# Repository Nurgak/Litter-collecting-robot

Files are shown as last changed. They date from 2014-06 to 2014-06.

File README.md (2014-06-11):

# STI interdisciplinary robot competition

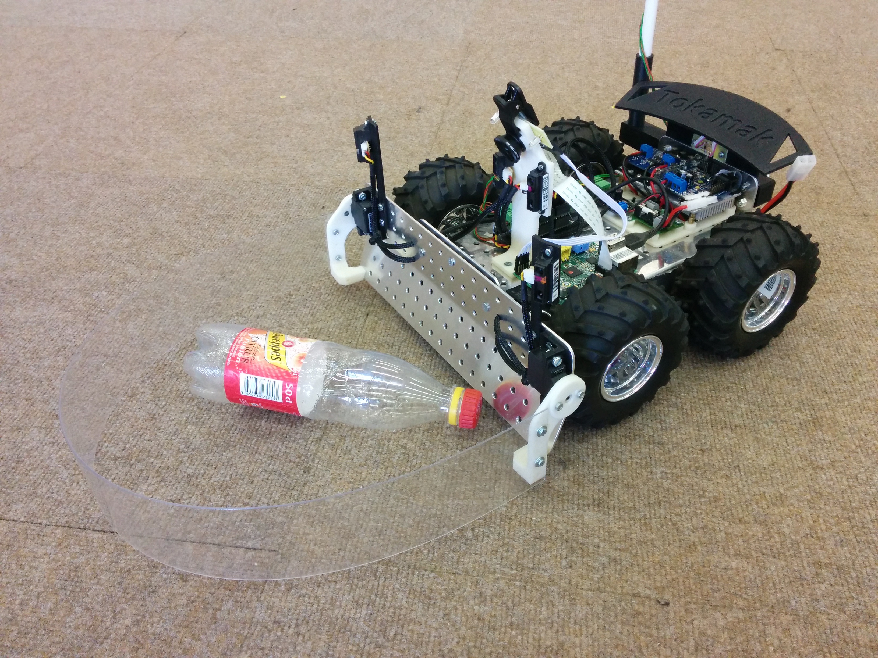
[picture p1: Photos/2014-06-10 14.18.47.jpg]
Tokamak


This project was completed as a Master semester project at [École polytechnique fédérale de Lausanne](http://www.epfl.ch).

* Authors: Karl Kangur, Marcel Starein, Chun Xie
* Assistants: Alessandro Crespi, Gorecki Tomasz
* Professor: Auke Ijspeert

## Abstract

The [STI competition](http://robot-competition.epfl.ch) is a interdisciplinary Master semester project in form of a competition between five teams of three people from different educational backgrounds. The competition's goal is to design and build a litter collecting robot and outperform the other robots. The teams are given funds in order to buy parts, order custom parts from the in-house mechanics or make use of the available 3D printers.

## Project report

The complete project report with all the documentation is in `Documents/Project report.pdf`.

## Video

[**Video of bottle fetching and detection demonstration**](https://www.youtube.com/watch?v=RZNW9JzXmiI)

## Pictures

See under `Photos`.

## Files

* All documents related to the project (rules, deadlines) and the project report itself are in `Documents`
* Documents related to sensors are under `Datasheets`
* First concepts in Google SketchUp, final parts in SolidWorks format and custom PCBs in `Hardware`
* The complete source code for the Raspberry Pi, Arduino code for the [PRsimino](https://github.com/Robopoly/prismino) and the custom WildThumper motor controller are in `Software`
* Pictures of the robot are under `Photos`
* The Webots files for the simulation are in `Webots simulation`

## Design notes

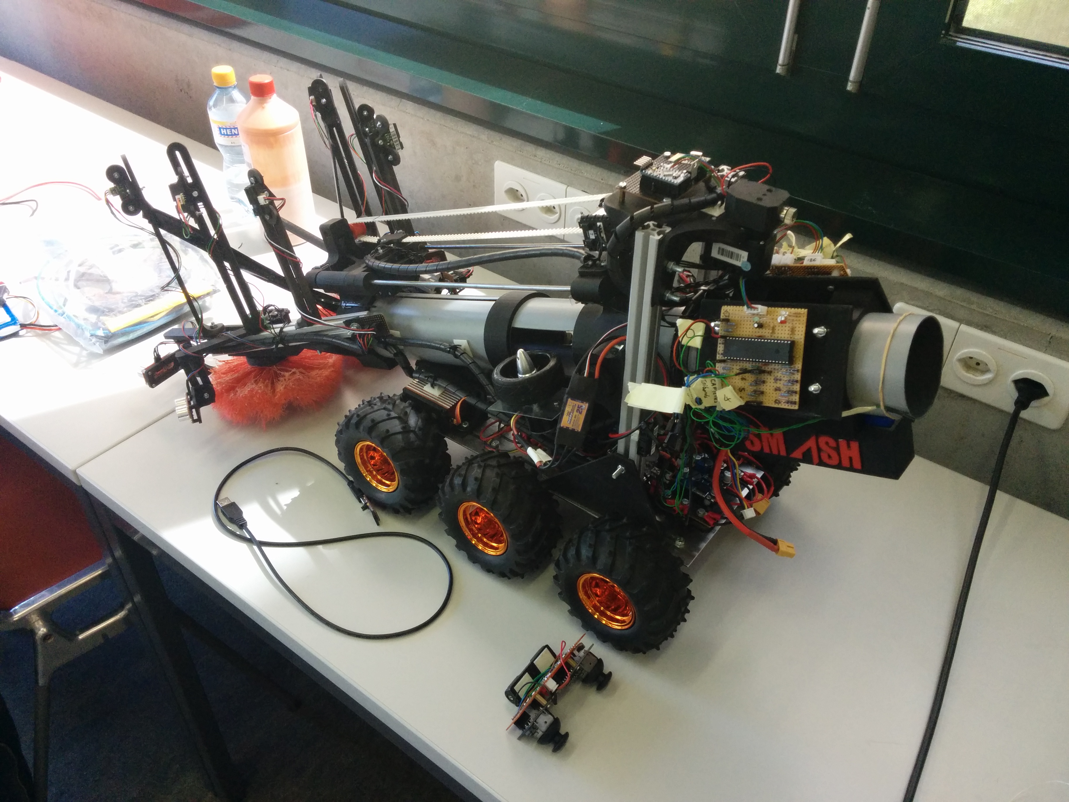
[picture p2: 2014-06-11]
Photos/2014-06-10 11.02.56.jpg

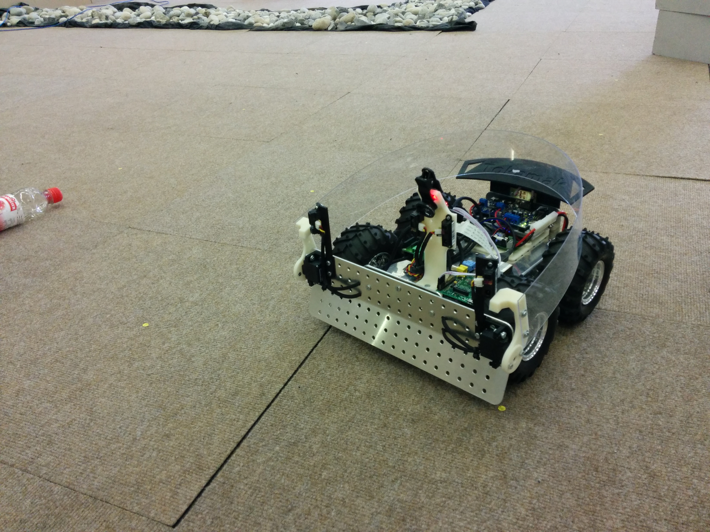
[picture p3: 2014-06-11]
Photos/2014-06-08 19.46.35.jpg

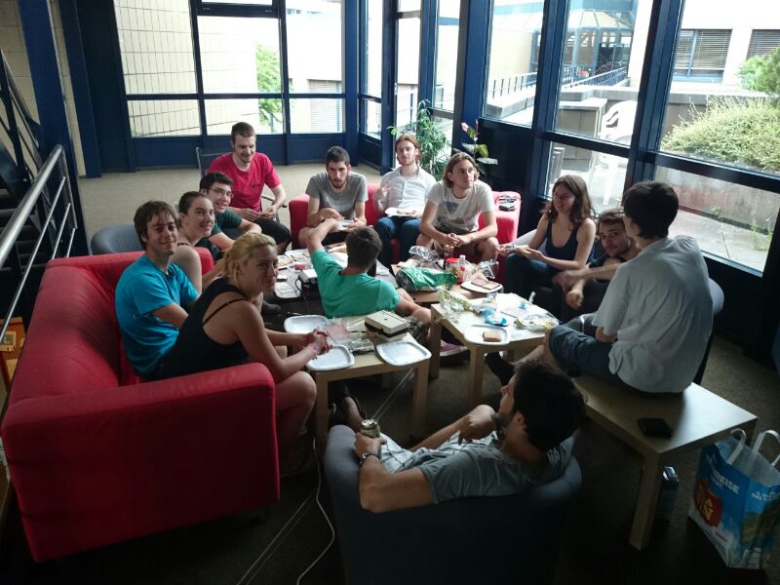
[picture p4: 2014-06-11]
Photos/IMG-20140609-WA0000.jpg

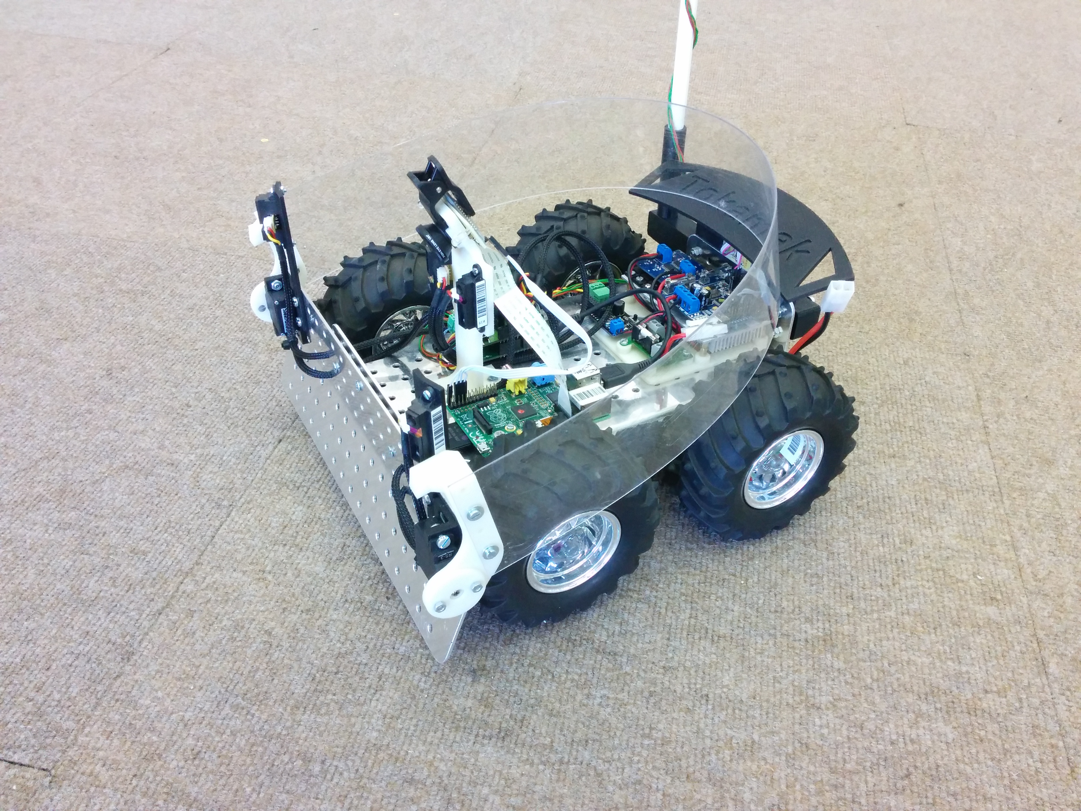
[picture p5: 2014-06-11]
Photos/2014-06-10 14.17.28.jpg

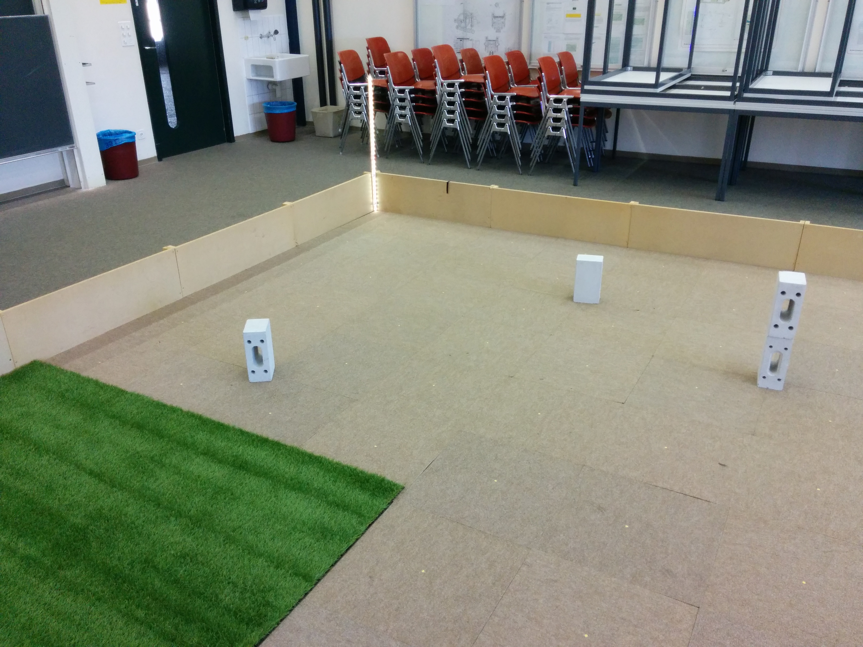
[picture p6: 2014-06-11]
Photos/2014-06-03 10.24.10.jpg

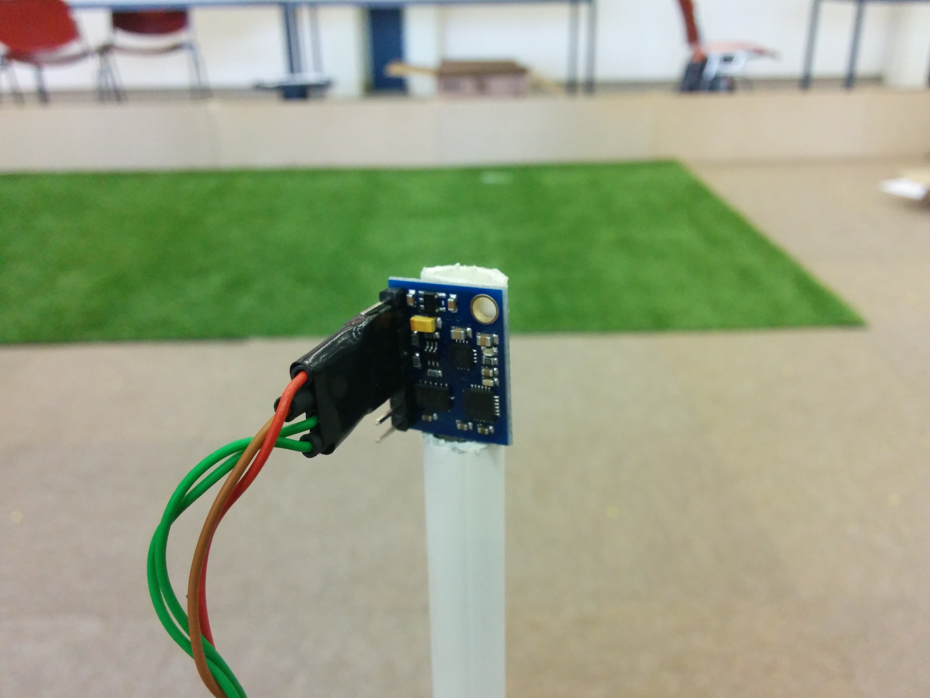
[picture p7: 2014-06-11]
Photos/2014-06-10 14.19.17.jpg

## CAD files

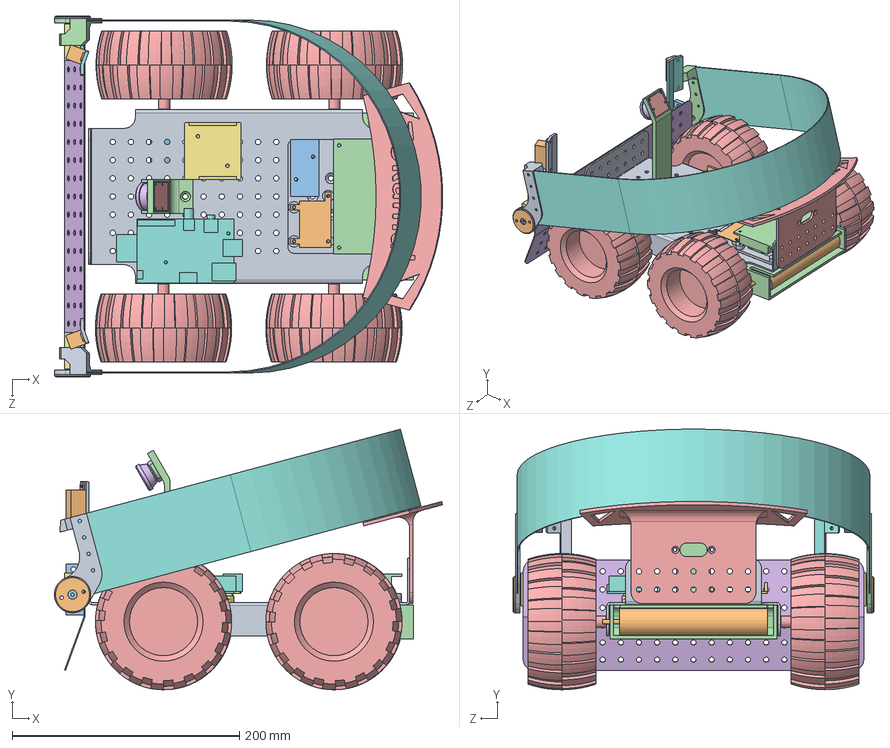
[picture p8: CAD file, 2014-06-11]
Hardware/SolidWorks files/Robot assembly/Robot assembly.SLDASM
341.8 x 229.4 x 317.8 mm
base
Battery
motor x 4
Motor controller
wheel x 4
plow
Servo motor x 2
Cage
H-bridge_support
Fuse board
Power board
Battery holder
hex nut style 1 gradeab_iso
PRismino support
PRismino
IR sensor support left
IR sensor support right
IR sensor x 2
Servo motor mount x 2
Camera support
Raspberry Pi camera
Lens
Raspberry Pi support
Raspberry Pi
Cage servo support left
Cage servo support blocker x 2
Servo adapter x 2
Cage servo support right
Cage rear support

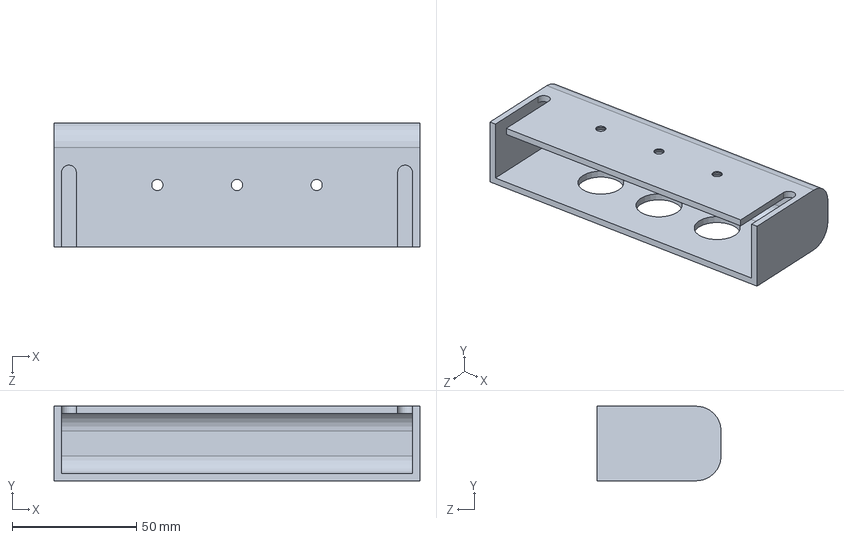
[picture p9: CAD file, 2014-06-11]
Hardware/SolidWorks files/Battery holder/Battery holder.SLDPRT
147.0 x 30.0 x 50.0 mm

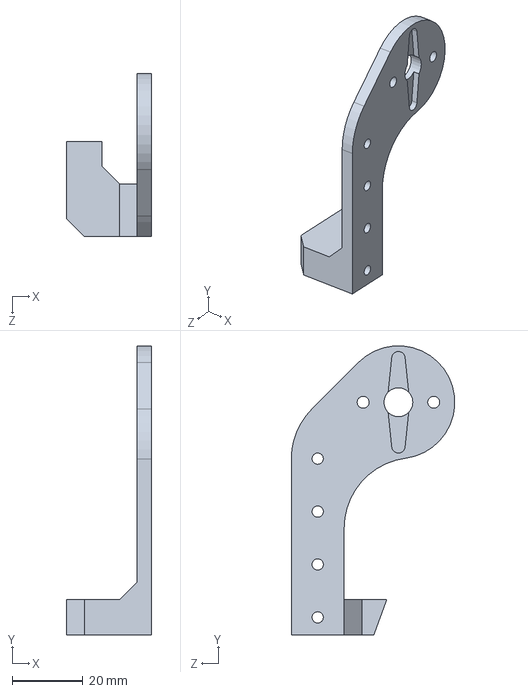
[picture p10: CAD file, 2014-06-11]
Hardware/SolidWorks files/Cage/Cage servo support left.SLDPRT
24.0 x 82.0 x 46.4 mm

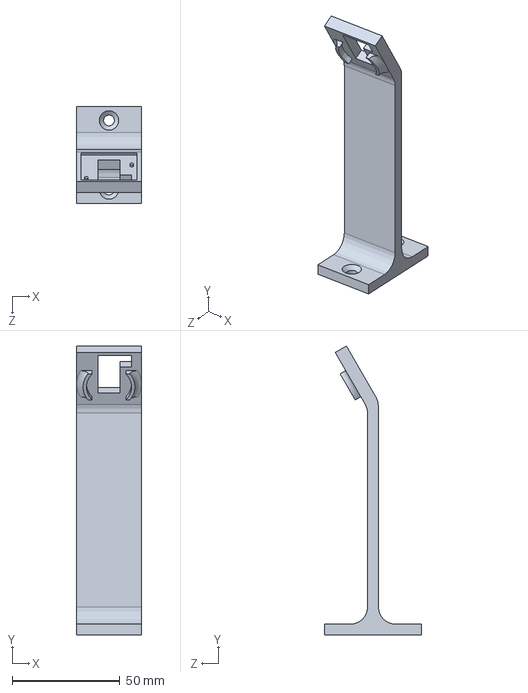
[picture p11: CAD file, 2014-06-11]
Hardware/SolidWorks files/Camera support/Camera support.SLDPRT
30.0 x 134.0 x 45.0 mm

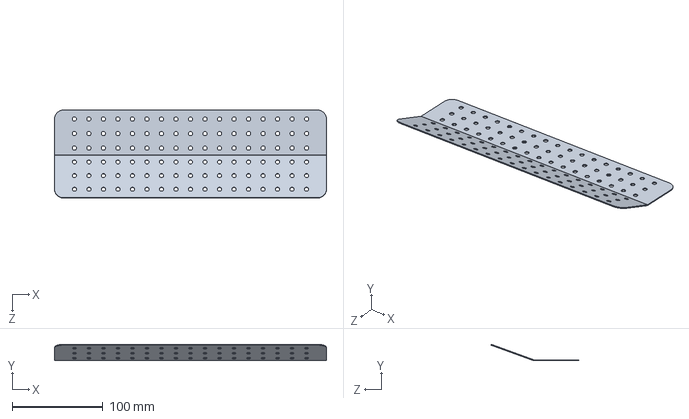
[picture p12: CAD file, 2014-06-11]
Hardware/SolidWorks files/Chassis/plow.SLDPRT
300.0 x 18.1 x 97.2 mm

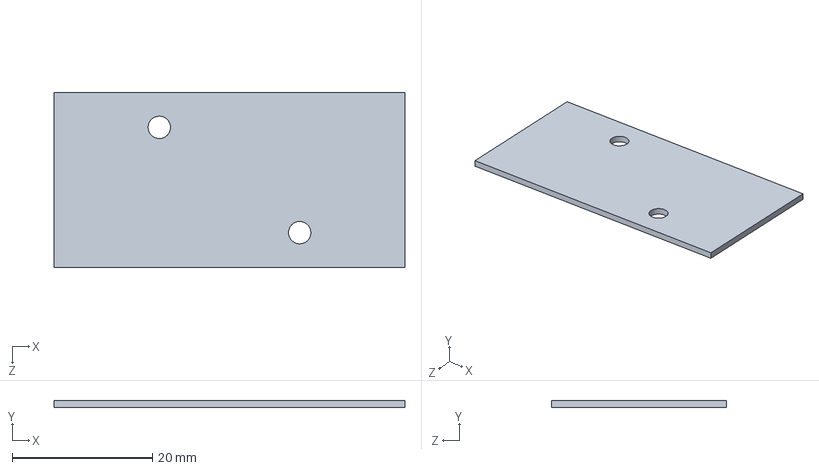
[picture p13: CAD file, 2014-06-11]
Hardware/SolidWorks files/H-bridge support/Power board.SLDPRT
50.0 x 1.06 x 25.0 mm

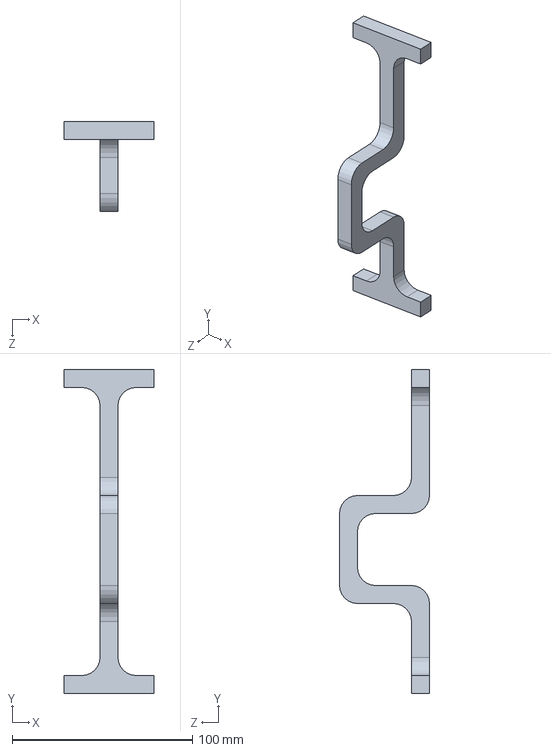
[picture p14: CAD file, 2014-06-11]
Hardware/SolidWorks files/IR sensor support/IR sensor support.SLDPRT
50.0 x 180.0 x 50.0 mm

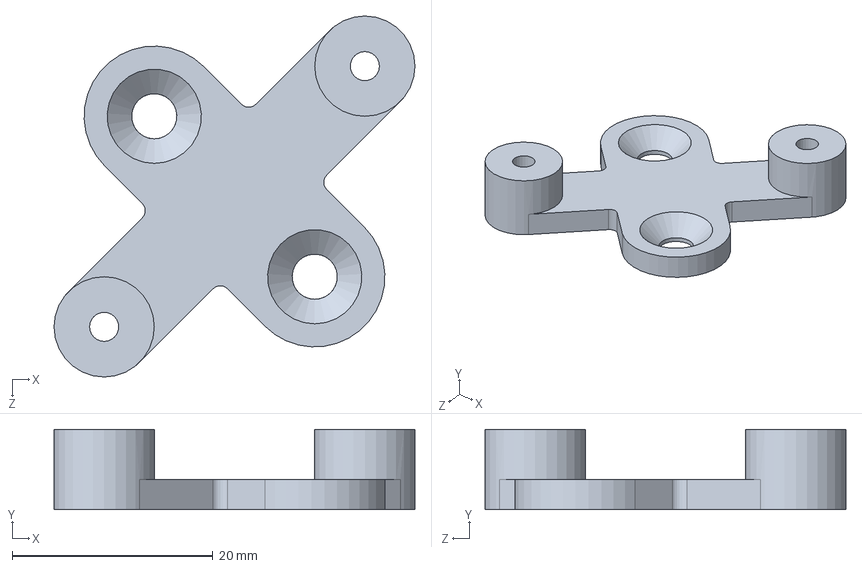
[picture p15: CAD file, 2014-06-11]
Hardware/SolidWorks files/PRismino/PRismino support.SLDPRT
36.0 x 8.00 x 36.0 mm

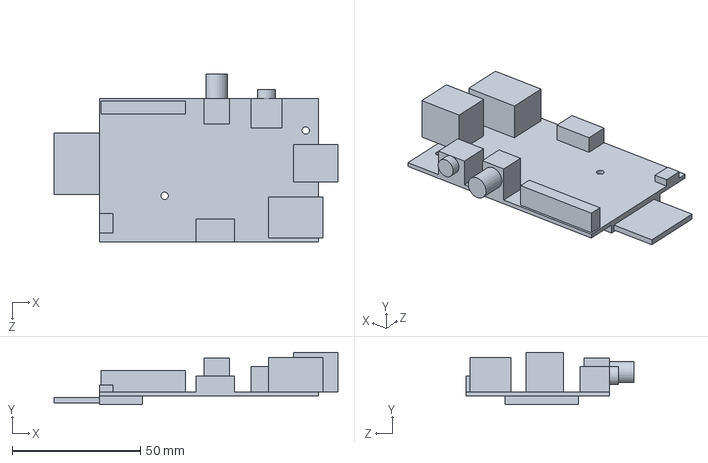
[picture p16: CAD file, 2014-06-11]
Hardware/SolidWorks files/Raspberry Pi support/Raspberry Pi.SLDPRT
110.9 x 20.5 x 65.5 mm

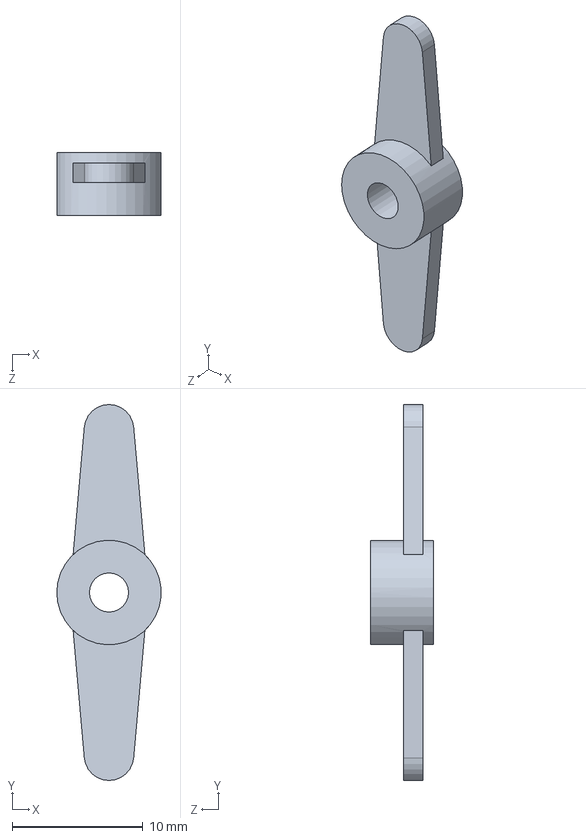
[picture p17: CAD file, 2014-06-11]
Hardware/SolidWorks files/Servo motor support/Servo adapter.SLDPRT
8.00 x 28.8 x 4.80 mm

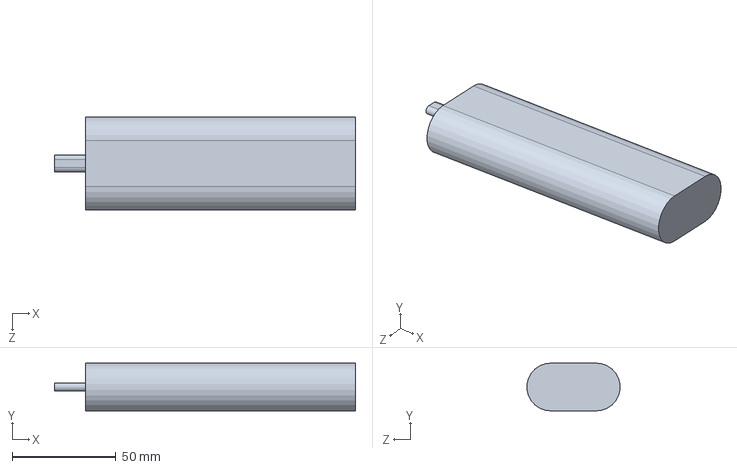
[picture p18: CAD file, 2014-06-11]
Hardware/SolidWorks files/Battery holder/Battery.SLDPRT
145.0 x 23.0 x 44.8 mm

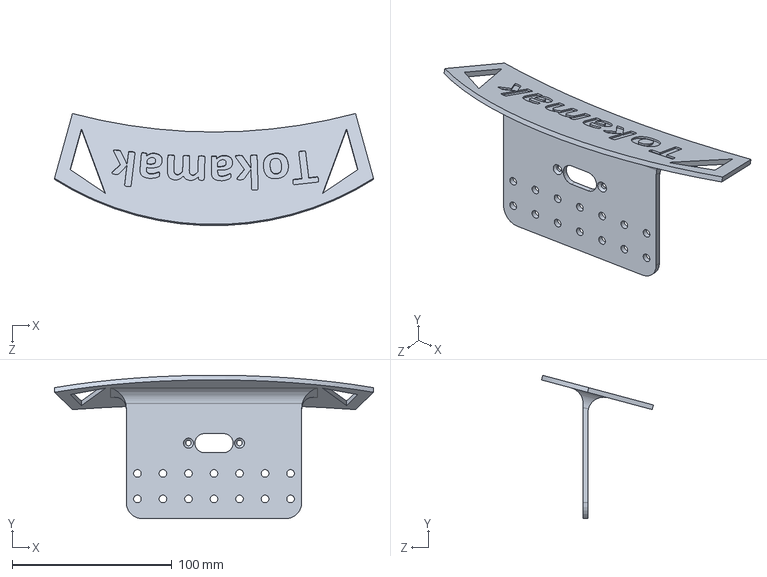
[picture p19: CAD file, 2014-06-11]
Hardware/SolidWorks files/Cage/Cage rear support.SLDPRT
200.0 x 89.9 x 70.2 mm

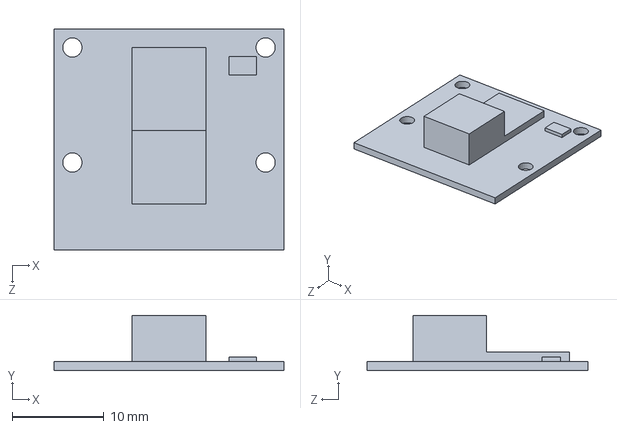
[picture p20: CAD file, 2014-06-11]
Hardware/SolidWorks files/Camera support/Raspberry Pi camera.SLDPRT
25.0 x 6.00 x 24.0 mm

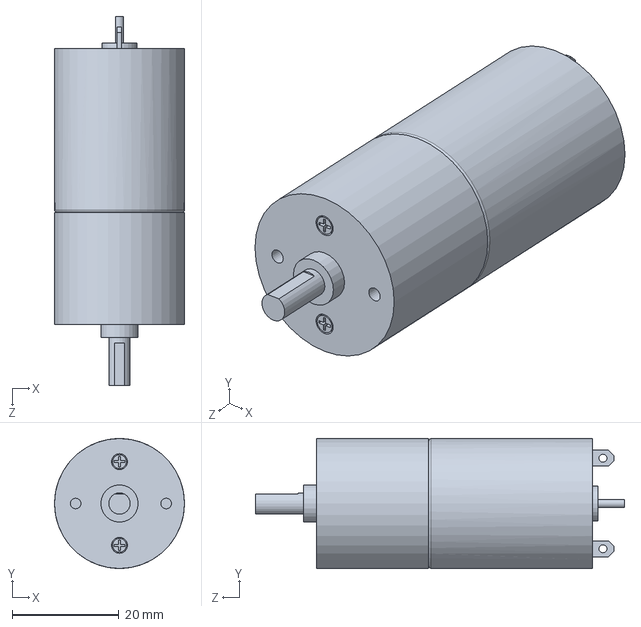
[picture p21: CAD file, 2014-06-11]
Hardware/SolidWorks files/Chassis/motor.SLDPRT
24.4 x 24.4 x 69.3 mm

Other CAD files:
Hardware/SolidWorks files/H-bridge support/H-bridge_support.SLDPRT
Hardware/SolidWorks files/IR sensor support/IR sensor support right.SLDPRT
Hardware/SolidWorks files/PRismino/PRismino.SLDPRT
Hardware/SolidWorks files/Raspberry Pi support/Raspberry Pi support.SLDPRT
Hardware/SketchUp/robot1.skp
Hardware/SketchUp/robot2.skp
Hardware/SketchUp/robot3.skp
Hardware/SolidWorks files/Cage/Cage rear support.STL
Hardware/SolidWorks files/Cage/Cage servo support blocker.SLDPRT
Hardware/SolidWorks files/Cage/Cage servo support blocker.STL
Hardware/SolidWorks files/Cage/Cage servo support left.STL
Hardware/SolidWorks files/Cage/Cage servo support right.SLDPRT
Hardware/SolidWorks files/Cage/Cage servo support right.STL
Hardware/SolidWorks files/Cage/Cage.SLDPRT
Hardware/SolidWorks files/Camera support/Lens.SLDPRT
Hardware/SolidWorks files/Chassis/base.SLDDRW
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

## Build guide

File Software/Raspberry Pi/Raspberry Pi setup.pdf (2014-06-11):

# Raspberry Pi setup

Configuration for the working environment based on the official Raspbian image.

## Basic configuration

$ sudo raspiconfig
Expand filesystem
Enable camera
Change timezone
Configure locales

To remove the language errors add the following lines to /etc/default/locale LANG=en_GB.UTF-8
LC_ALL=en_GB.UTF-8
LANGUAGE=en_GB.UTF-8

Then reboot the system
$ sudo reboot

Update the system
$ sudo aptget update
$ sudo aptget upgrade
$ sudo reboot

Update the firmware
$ sudo rpiupdate
$ sudo reboot

## Public key authentication (optional)

On a mac transfer the public key to the RPi
$ cat ~/.ssh/id_rsa.pub | ssh pi@192.168.0.28 "mkdir .ssh;cat >> .ssh/authorized_keys"

## Camera driver installation (for C++)

$ wget http://www.linuxprojects.org/listing/uv4l_repo/lrkey.asc && sudo aptkey add ./lrkey.asc

Add the following line to the file /etc/apt/sources.list
$ deb http://www.linuxprojects.org/listing/uv4l_repo/raspbian/ wheezy main
$ sudo aptget update
$ sudo aptget install uv4l uv4lraspicam
$ sudo reboot

For driver options type
$ uv4l help driver raspicam driverhelp

To load the driver
$ uv4l driver raspicam autovideo_nr width 640 height 480 nopreview encoding jpeg

Or
$ uv4l driver raspicam autovideo_nr width 640 height 480 nopreview encoding yuv420

To load the driver at boot
$ sudo aptget install uv4lraspicamextras

To kill the driver
$ pkill uv4l

## OpenCV installation

This installs the required packages for C/C++ and Python OpenCV programming, if only C/C++ is required then “libopencvdev” is enough.

$ sudo aptget install libopencvdev pythonopencv

Depending on the use the uv4l driver may need to be loaded and the LD_PRELOAD may need to be defined, but this maybe not, try without these 2 lines first:

$ uv4l driver raspicam autovideo_nr width 640 height 480 nopreview encoding jpeg
$ export LD_PRELOAD=/usr/lib/uv4l/uv4lext/armv6l/libuv4lext.so

## Camera API in Python

This package uses MMAL underneath and is extremely fast in acquiring the preview image, it also doesn’t need the driver and LD_PRELOAD to be defined and is really easy to use and configure.

$ sudo aptget install pythonpicamera

http://picamera.readthedocs.org/en/release-1.3/install2.html#raspbianinstallation

## Camera API in C++

This works, really fast, but only in grayscale.

See https://github.com/Josh-Larson/CameraBoardAPI (https://github.com/Josh-Larson/CameraBoardAPI)

Copy the files “/build/src/libraspicam.so*” into /usr/local/lib/.

Other resources:
- https://github.com/tasanakorn/rpimmaldemo (https://github.com/tasanakorn/rpi-mmal-demo)
- https://github.com/hcpa/rpimmalcam (https://github.com/hcpa/rpi-mmalcam)

## Access desktop with VNC

$ sudo aptget update
$ sudo aptget install tightvncserver

To start the VNC server type

$ vncserver
Enter an 8 character password such as “12345678”
Select “n” for viewonly password

To connect from a Mac computer open Finder, go to Go→Connect to Server… (⌘K) and type vnc://<IP of the RPi>:5901

## I2C communication

Install: http://skpang.co.uk/blog/archives/575

$ sudo aptget update
$ sudo aptget install i2ctools

It’s normal to get the “/run/udev or .udevdb or .udev presence implies active udev. Aborting MAKEDEV invocation.” warning, it doesn’t mean there was an error in the install.

Add “pi” to the group “i2c” to get the permissions to use the i2ctools:
$ sudo adduser pi i2c
$ sudo reboot

To detect if something is connected to the i2c lines type:
$ sudo i2cdetect y 1

Examples: http://www.robotelectronics.co.uk/htm/raspberry_pi_examples.htm (http://www.robot-electronics.co.uk/htm/raspberry_pi_examples.htm)

Make sure not to go over 3.3V on the RPi GPIO pins, if the Arduino Wire library is used it automatically activates the pullup resistors to its VCC which can be at 5V.

## Serial connection in C++

To connect to a USB device via the serial connection there is no need to install anything, the USB device (an Arduino for example) will be visible in /dev/ttyACM0, one should simply connect to it via a serial console or through a C++ program.

To test the connection you can use the screen command:
$ sudo aptget update
$ sudo aptget install screen
$ screen /dev/ttyACM0 9600

Type Alt+a, Alt+k to exit screen.

## Serial connection in Python

http://pyserial.sourceforge.net/

$ sudo aptget install pythonserial

## Raspberry Pi LED control

One can control the onboard ACT LED for debugging: http://raspberrypi.stackexchange.com/questions/697/howdoicontrolthesystemledsusingmys oftware (http://raspberrypi.stackexchange.com/questions/697/how-do-i-control-the-system-leds-using-my-software)

$ sudo su
$ echo none >/sys/class/leds/led0/trigger
$ echo 1 >/sys/class/leds/led0/brightness
$ echo 0 >/sys/class/leds/led0/brightness
$ exit

The LED is connected to GPIO16 which can be used to toggle the LED when not used for SD card access indication.

Reset to default ACT function which makes it come on when the SD card is accessed:
$ echo mmc0 >/sys/class/leds/led0/trigger

## Mount the Raspberry Pi filesystem in read-only

To prevent corruption the filesystem can be mounted in readonly mode so that a power failure won’t corrupt the system if it was currently writing something on the SD card.

In /etc/fstab:
/dev/mmcblk0p2 / | ext4 defaults,noatime,ro 0 | 1
tmpfs | /tmp | tmpfs defaults,size=30M 0 | 0

Disable services you don’t need (not tested):
insserv r dphysswapfile
insserv r rsyslog

http://raspberrypi.stackexchange.com/questions/5112/runningonreadonlysdcard

## WiFi configuration from command line

When a WiFi dongle is attached and must be configured via serial, such as Bluetooth, these are the commands to issue: http://harindern.blogspot.ch/2013/02/raspberrywifi.html

Other good tutorial: http://www.maketecheasier.com/setupwifionraspberrypi/ (http://www.maketecheasier.com/setup-wifi-on-raspberry-pi/)

Make sure all lines perfectly match, sometimes some line breaks are skipped when opening a file for some reason, they must be put back before saving.

## Ethernet connection directly with the Raspberry Pi

To connect 2 computers via Ethernet cable they have to be assigned IP addresses.

First conigure the Rapsberry Pi with a static address the the following command: $ sudo ifconfig eth0 192.168.0.10

Then configure the comptuer (Linux) with
$ sudo ifconfig eth0 192.168.0.1

The computer will be able to communicate with the Raspberry Pi via ssh now.

## Launch python script at startup

Add these lines before “exit 0” in /ets/rc.local

# Automatically launch the robot script python /home/pi/robot/python/control.py &

## References

- Another C++ API for the camera http://www.uco.es/investiga/grupos/ava/node/40
- Acquiring full sensor video with a Raspberry Pi camera module using v4l2 http://www.robertcudmore.org/blog/?p=200

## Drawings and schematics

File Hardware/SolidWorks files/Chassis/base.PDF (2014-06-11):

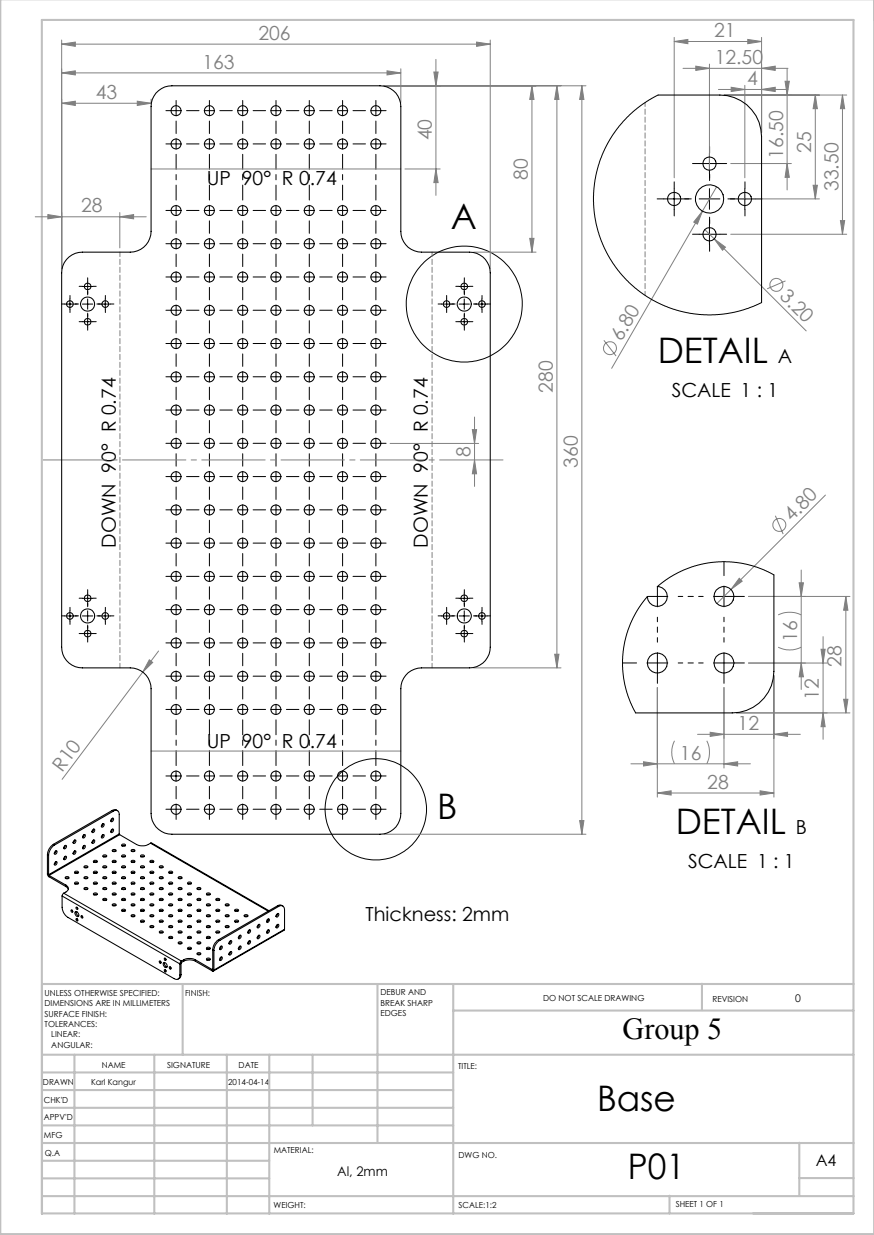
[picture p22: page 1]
DOWN 90° R 0.74; DETAIL A; SCALE 1 : 1; DETAIL B; Thickness: 2mm; Group 5; SCALE:1:2; SHEET 1 OF 1; DO NOT SCALE DRAWING; REVISION; DEBUR AND BREAK SHARP; UNLESS OTHERWISE SPECIFIED:; FINISH:

DIMENSIONS ARE IN MILLIMETERS
SURFACE FINISH:
TOLERANCES:
LINEAR:
ANGULAR:

NAME | SIGNATURE | DATE | | | | TITLE: Base
Q.A | | | | MATERIAL: Al, 2mm | P01 DWG NO. | A4

DRAWN | Karl Kangur | | 2014-04-14
CHK'D
APPV'D
MFG

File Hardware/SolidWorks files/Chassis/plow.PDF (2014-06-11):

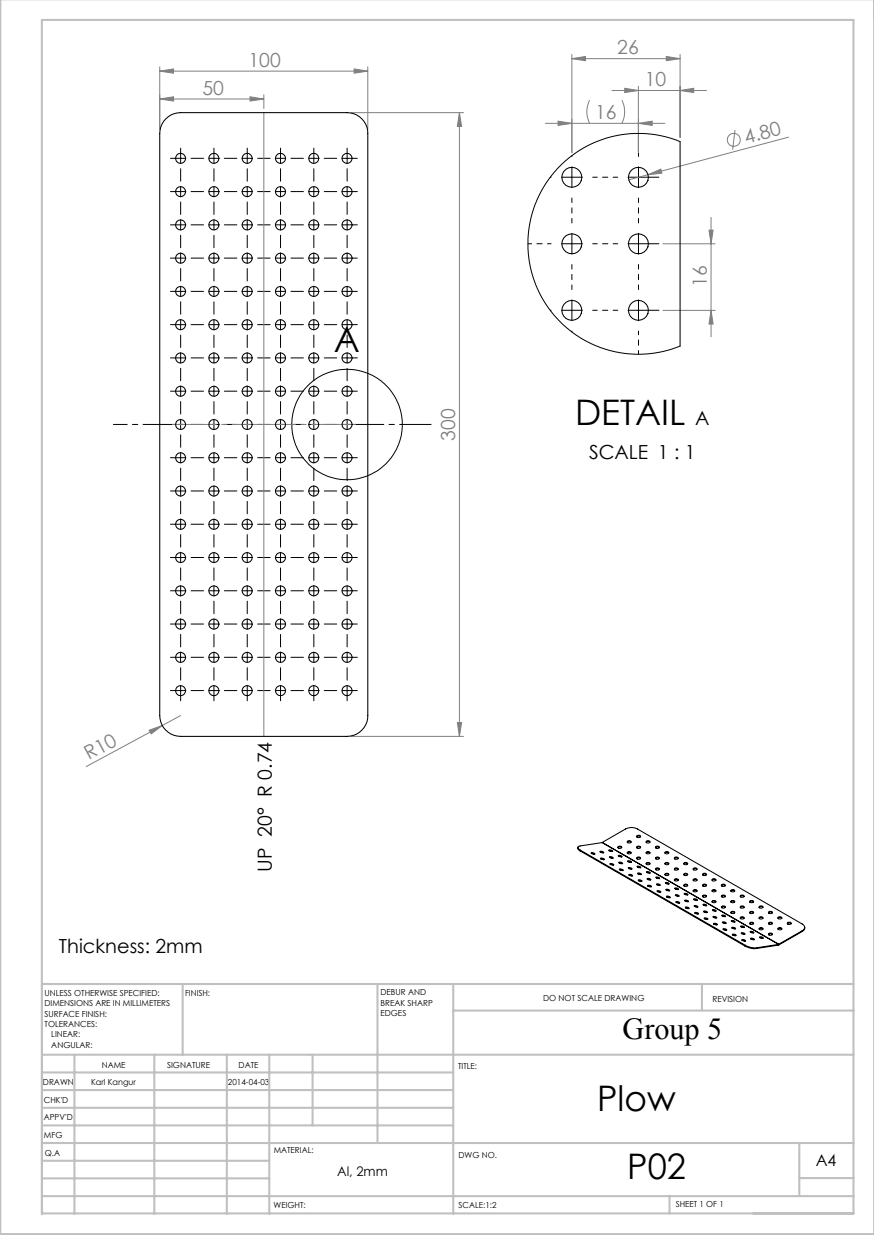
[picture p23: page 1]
DETAIL A; SCALE 1 : 1; Thickness: 2mm; Group 5; SCALE:1:2; SHEET 1 OF 1; DO NOT SCALE DRAWING; REVISION; DEBUR AND BREAK SHARP; UNLESS OTHERWISE SPECIFIED:; FINISH:

DIMENSIONS ARE IN MILLIMETERS
SURFACE FINISH:
TOLERANCES:
LINEAR:
ANGULAR:

NAME | SIGNATURE | DATE | | | | TITLE: Plow
Q.A | | | | MATERIAL: Al, 2mm | P02 DWG NO. | A4

DRAWN | Karl Kangur | | 2014-04-03
CHK'D
APPV'D
MFG

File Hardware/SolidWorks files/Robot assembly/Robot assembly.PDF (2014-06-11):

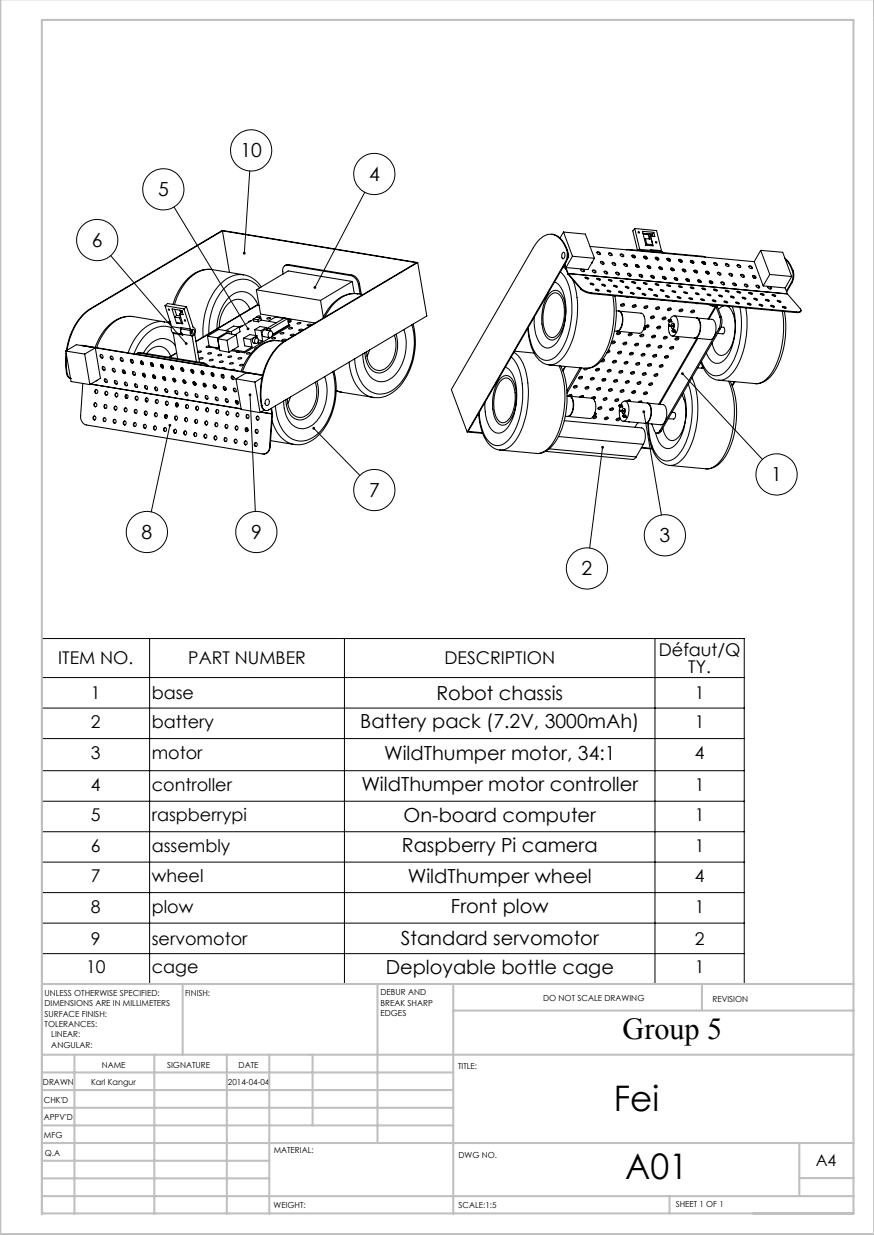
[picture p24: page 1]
Group 5; SCALE:1:5; SHEET 1 OF 1

ITEM NO. | PART NUMBER | DESCRIPTION | Défaut/Q TY.
1 | base | Robot chassis | 1
2 | battery | Battery pack (7.2V, 3000mAh) | 1
3 | motor | WildThumper motor, 34:1 | 4
4 | controller | WildThumper motor controller | 1
5 | raspberrypi | On-board computer | 1
6 | assembly | Raspberry Pi camera | 1
7 | wheel | WildThumper wheel | 4
8 | plow | Front plow | 1
9 | servomotor | Standard servomotor | 2
10 | cage | Deployable bottle cage | 1

UNLESS OTHERWISE SPECIFIED: DIMENSIONS ARE IN MILLIMETERS SURFACE FINISH: TOLERANCES: LINEAR: ANGULAR: | FINISH: | DEBUR AND BREAK SHARP EDGES | DO NOT SCALE DRAWING | REVISION
NAME | SIGNATURE | DATE | | | | TITLE: Fei
Q.A | | | | MATERIAL: | A01 DWG NO. | A4

DRAWN | Karl Kangur | | 2014-04-04
CHK'D
APPV'D
MFG

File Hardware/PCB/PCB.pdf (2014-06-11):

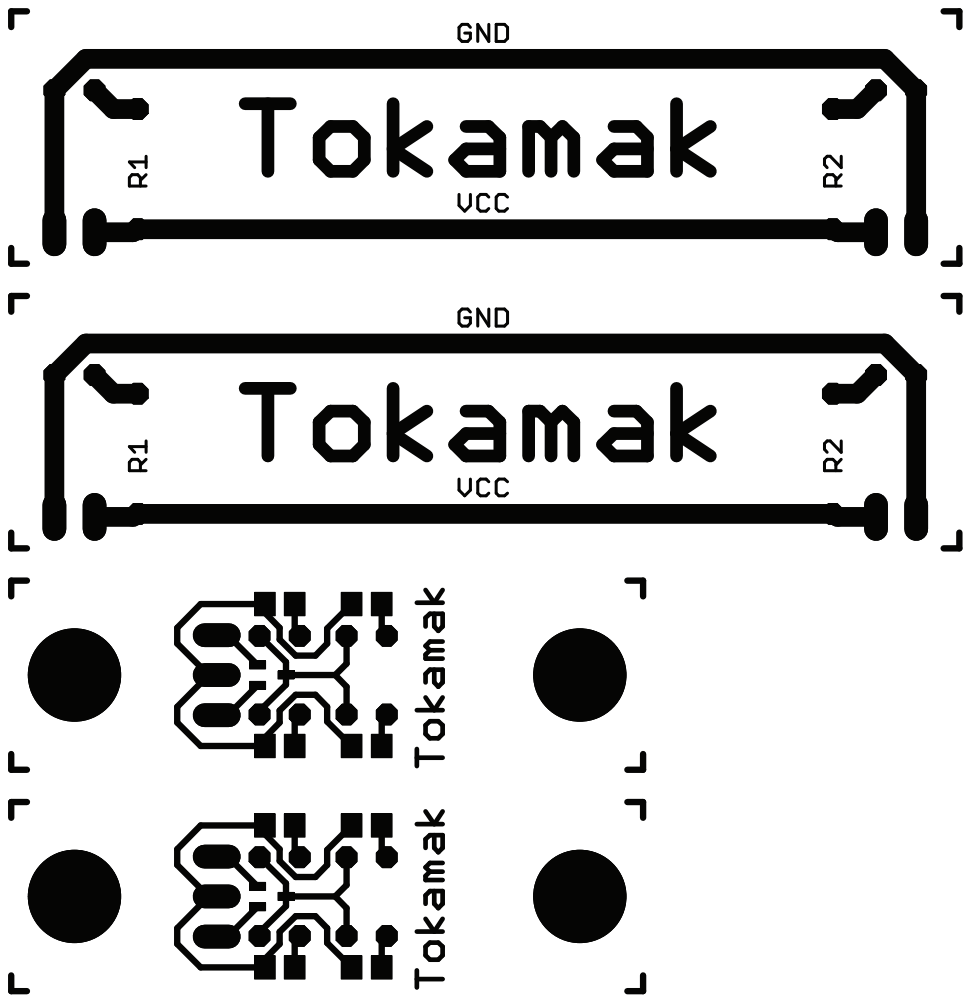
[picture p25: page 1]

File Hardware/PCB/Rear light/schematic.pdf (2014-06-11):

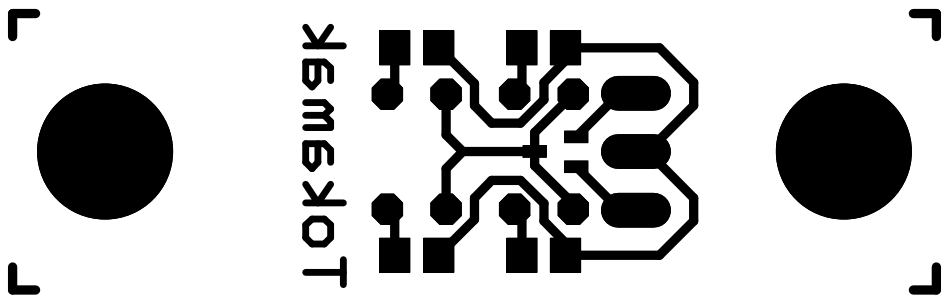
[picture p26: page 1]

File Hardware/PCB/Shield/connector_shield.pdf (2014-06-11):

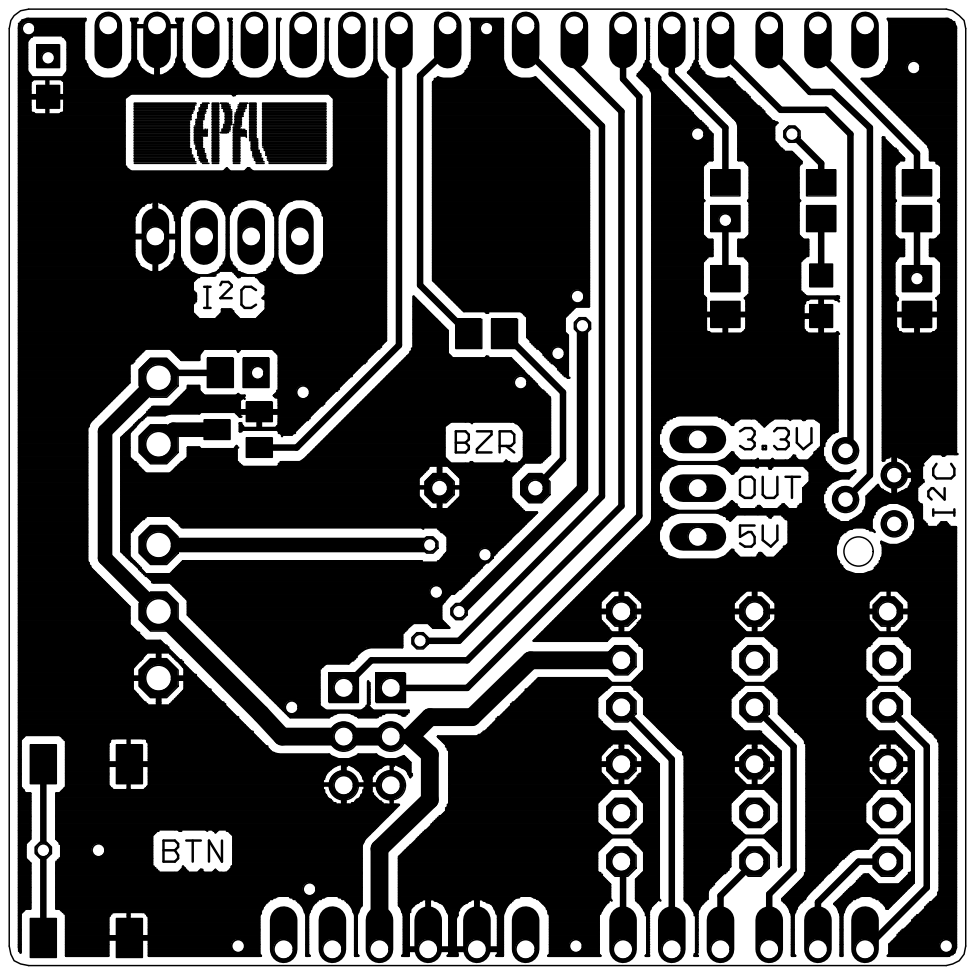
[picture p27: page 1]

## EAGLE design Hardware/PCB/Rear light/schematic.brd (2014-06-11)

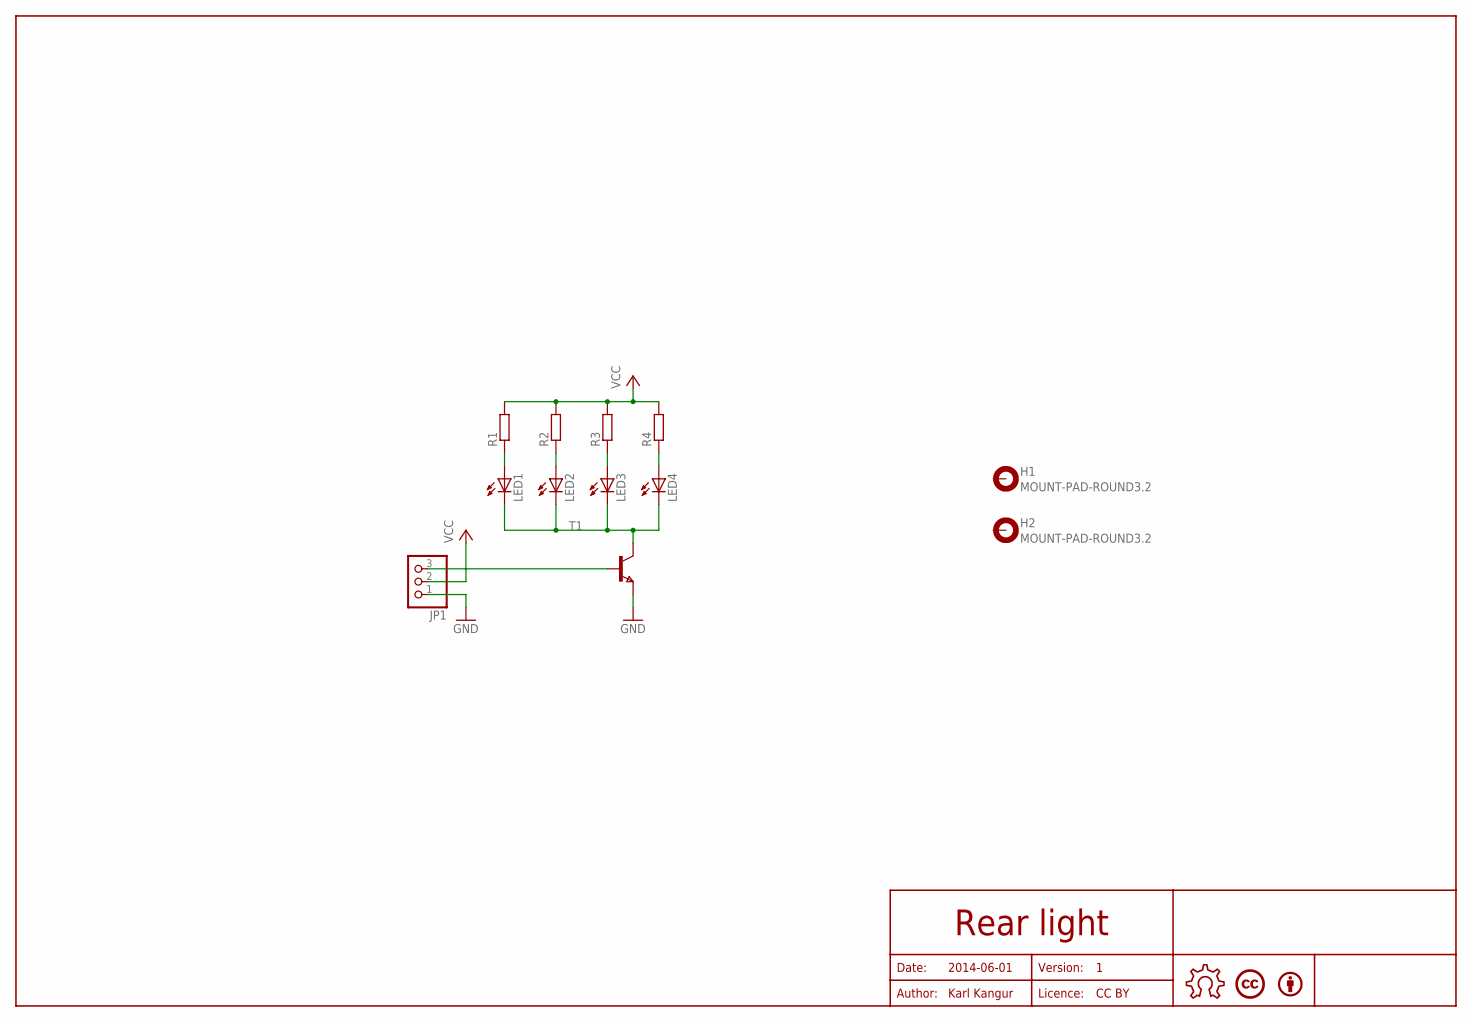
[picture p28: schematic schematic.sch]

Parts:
BY1: BYBOTTOM; BY
H1, H2: MOUNT-PAD-ROUND3.2; 3,2-PAD
JP1: PINHD-1X3; 1X03
LED1, LED2, LED3, LED4: LED3MM
LICENCE1: LICENCECC-BOTTOM; CREATIVE-COMMONS
R1, R2, R3, R4: R-EU_R0805; R0805
T1: NPNSOT323; SOT323
U$10: OPEN-HARDWARE-LOGOBOTTOM-SMALL; OPEN-HARDWARE-BOTTOM-SMALL

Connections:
GND: JP1.1, T1.3 (E)
unnamed: JP1.3, T1.2 (B)
unnamed: LED1.K (C), LED2.K (C), LED3.K (C), LED4.K (C), T1.1 (C)
unnamed: LED1.A, R1.1
unnamed: LED2.A, R2.1
unnamed: LED3.A, R3.1
unnamed: LED4.A, R4.1
VCC: JP1.2, R1.2, R2.2, R3.2, R4.2

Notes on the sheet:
Date:
Author:
Licence:
Version:
2014-06-01
Karl Kangur
CC BY
Rear light

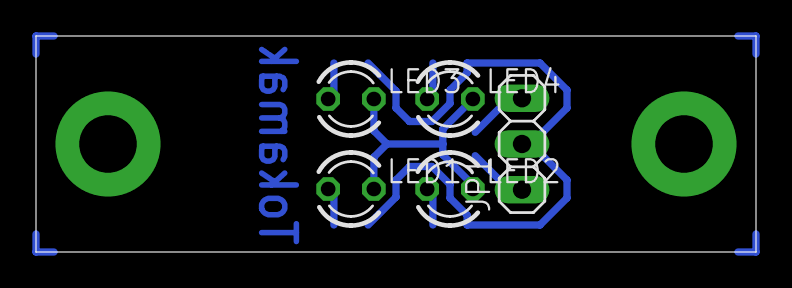
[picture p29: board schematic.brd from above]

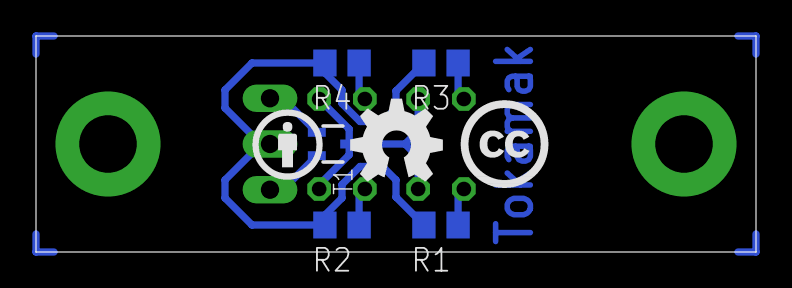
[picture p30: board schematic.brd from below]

Board: 2 copper layers, 40.0 x 12.0 mm, 15 parts (5 on the bottom side), 8 nets.

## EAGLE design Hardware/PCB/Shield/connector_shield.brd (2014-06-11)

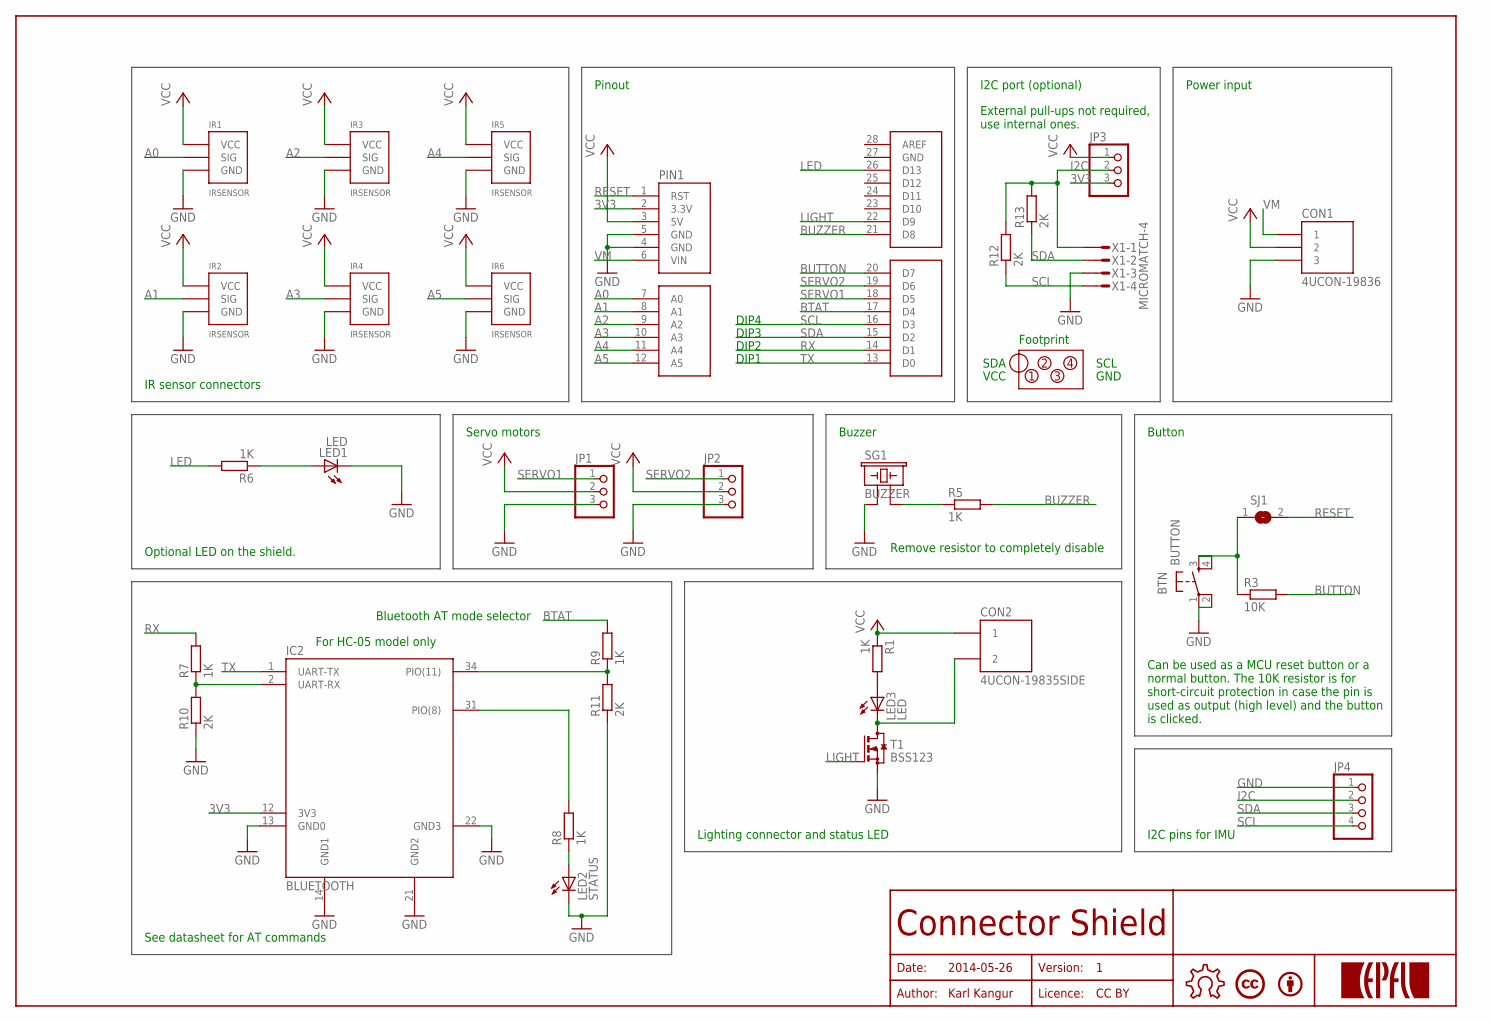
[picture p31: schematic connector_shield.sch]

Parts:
BTN: BUTTON
BY1: BYBOTTOM; BY
CON1: 4UCON-19836
CON2: 4UCON-19835SIDE; 4UCON-19835
IC2: BLUETOOTH
IR1, IR2, IR3, IR4, IR5, IR6: IRSENSOR; A-6373-03
JP1, JP2, JP3: PINHD-1X3; 1X03
JP4: PINHD-1X4; 1X04
LED1, LED3: LED; CHIPLED_0805
LED2: STATUS; CHIPLED_0805
LICENCE1: LICENCECC-BOTTOM; CREATIVE-COMMONS
PIN1: ARDUINOSTACK; ARDUINO-LONG
R1, R5, R6, R7, R8, R9: 1K; R0805
R3: 10K; R0805
R10, R11, R12, R13: 2K; R0805
SG1: BUZZER; PS1240P02BT
SJ1: SJ
T1: BSS123; SOT23
U$10: OPEN-HARDWARE-LOGOBOTTOM-SMALL; OPEN-HARDWARE-BOTTOM-SMALL
U$11: EPFL-LOGO; EPFL-LOGO-PCB
X1: MICROMATCH-4

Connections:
3V3: IC2.12 (3V3), JP3.3, PIN1.2 (3.3V)
A0: IR1.SIG, PIN1.7 (A0)
A1: IR2.SIG, PIN1.8 (A1)
A2: IR3.SIG, PIN1.9 (A2)
A3: IR4.SIG, PIN1.10 (A3)
A4: IR5.SIG, PIN1.11 (A4)
A5: IR6.SIG, PIN1.12 (A5)
BTAT: PIN1.17 (D4), R9.2
BUTTON: PIN1.20 (D7), R3.2
BUZZER: PIN1.21 (D8), R5.2
GND: BTN.1, BTN.2, CON1.3, IC2.13 (GND0), IC2.14 (GND1), IC2.21 (GND2), IC2.22 (GND3), IR1.GND, IR2.GND, IR3.GND, IR4.GND, IR5.GND, IR6.GND, JP1.3, JP2.3, JP4.1, LED1.C, LED2.C, PIN1.4 (GND), PIN1.5 (GND), PIN1.27 (GND), R10.1, R11.1, SG1.P$1 (1), T1.2 (S), X1.3
I2C: JP3.2, JP4.2, R12.2, R13.2, X1.1
LED: PIN1.26 (D13), R6.2
LIGHT: PIN1.22 (D9), T1.1 (G)
unnamed: CON2.2, LED3.C, T1.3 (D)
unnamed: IC2.31 (PIO(8)), R8.2
unnamed: LED2.A, R8.1
unnamed: LED3.A, R1.2
unnamed: R5.1, SG1.P$2 (2)
unnamed: IC2.34 (PIO(11)), R9.1, R11.2
unnamed: LED1.A, R6.1
unnamed: BTN.3, BTN.4, R3.1, SJ1.1
unnamed: IC2.2 (UART-RX), R7.1, R10.2
RESET: PIN1.1 (RST), SJ1.2
RX: PIN1.14 (D1), R7.2
SCL: JP4.4, PIN1.16 (D3), R12.1, X1.4
SDA: JP4.3, PIN1.15 (D2), R13.1, X1.2
SERVO1: JP1.1, PIN1.18 (D5)
SERVO2: JP2.1, PIN1.19 (D6)
TX: IC2.1 (UART-TX), PIN1.13 (D0)
VCC: CON1.2, CON2.1, IR1.VCC, IR2.VCC, IR3.VCC, IR4.VCC, IR5.VCC, IR6.VCC, JP1.2, JP2.2, JP3.1, PIN1.3 (5V), R1.1
VM: CON1.1, PIN1.6 (VIN)

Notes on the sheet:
Date:
Author:
Licence:
Version:
2014-05-26
Karl Kangur
CC BY
Connector Shield
Pinout
I2C port (optional)
Buzzer
Servo motors
Button
DIP1
DIP2
DIP3
DIP4
Power input
See datasheet for AT commands
Footprint
VCC
SDA
SCL
GND
Bluetooth AT mode selector
For HC-05 model only
Can be used as a MCU reset button or a normal button. The 10K resistor is for short-circuit protection in case the pin is used as output (high level) and the button is clicked.
Optional LED on the shield.
External pull-ups not required, use internal ones.
Remove resistor to completely disable
Lighting connector and status LED
IR sensor connectors
I2C pins for IMU

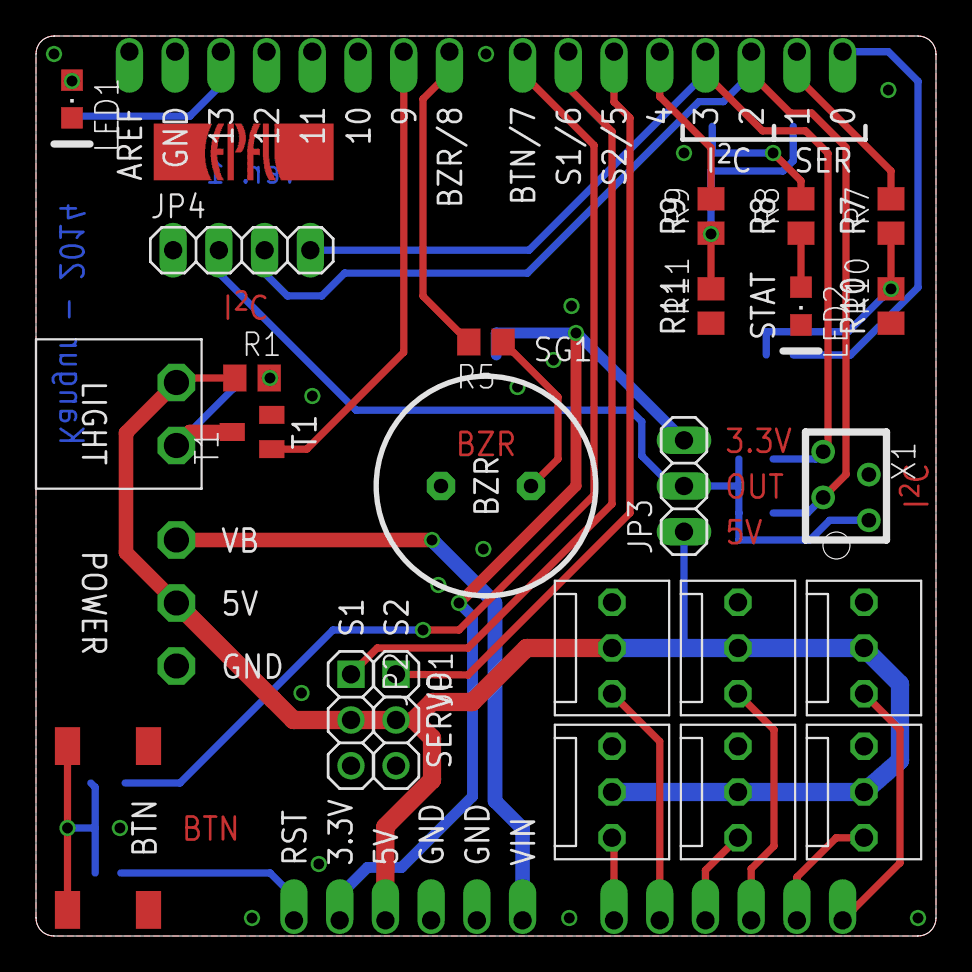
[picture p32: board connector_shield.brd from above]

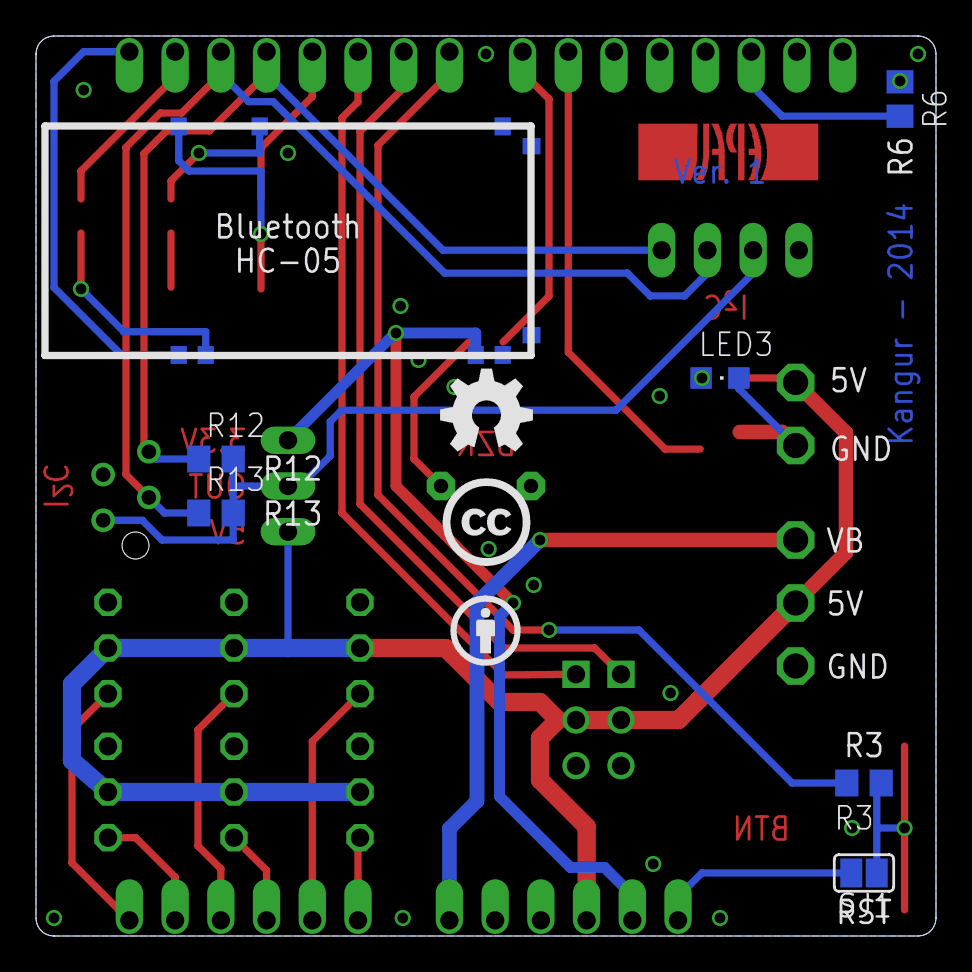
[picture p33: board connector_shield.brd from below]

Board: 2 copper layers, 50.0 x 50.0 mm, 37 parts (7 on the bottom side), 32 nets.

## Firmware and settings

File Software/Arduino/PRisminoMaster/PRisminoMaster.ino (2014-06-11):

/***************************************************************************************
 *
 * Title:      PRismino I2C master sketch communicating with the Raspberry Pi via
 *             serial and the motor controller via I2C.
 * Date:       2014-06-04
 *
 ***************************************************************************************/
#include <Wire.h>
#include <prismino.h>
#include <Servo.h>
//#include <Bluetooth.h>
#include "I2Cdev.h"
#include "MPU6050.h"
#include "PRisminoMaster.h"

#define Bluetooth Serial1

// comment this line when testing without the motor controller
#define ENABLE_CONTROLLER
// comment this line to permanently disable all Bluetooth functionalities
#define ENABLE_BLUETOOTH

// IMU object instance
MPU6050 imu;

enum cage_positions cagePos = CAGE_UP;

Servo servoLeft;
Servo servoRight;

uint16_t batteryVoltage, currentLeft, currentRight;
uint16_t Z_MAX = 500, Z_MIN=100, X_MAX=500, X_MIN=100;
uint8_t ip[4] = {0, 0, 0, 0};
char buffer[16];
uint8_t enableAutoObstacleAvoidance = 0;
uint8_t enableFrontLeds = 0;
uint8_t enableSerialDumpIrValues = 0;
uint8_t wallSide=0;
uint8_t goHomeValue=0;



#ifdef ENABLE_CONTROLLER
uint32_t timeCheckBattery = 0;
uint32_t timeAntiLoop = 0;
#endif

#ifdef ENABLE_BLUETOOTH
char serialData[32];
#endif

void setup()
{
  // set pin output mode (sources current)
  pinMode(LED, OUTPUT);
  pinMode(PIN_LIGHTS, OUTPUT);
  
  // enable button pull-up
  pinMode(BTN, INPUT);
  digitalWrite(BTN, HIGH);

  // play a sound on boot, repeated sounds will indicate very low battery voltage
  play(TONE_BEEP, 500);

  // initialise serial bus for communication with the Raspberry Pi
  Serial.begin(9600);

  // initialise the bus for communication with the coimuter via Bluetooth
  #ifdef ENABLE_BLUETOOTH
  Bluetooth.begin(9600);
  #endif

  // join i2c bus (as master)
  Wire.begin();
  digitalWrite(SDA, LOW);
  digitalWrite(SCL, LOW);
  
  //Put the HMC5883 IC into the correct operating mode
  Wire.beginTransmission(I2C_COMPASS_ADDRESS); //open communication with HMC5883
  Wire.write(0x02); //select mode register
  Wire.write(0x00); //continuous measurement mode
  Wire.endTransmission();

  // request data from the motor controller as first handshake, this will inform of any i2c bus errors via a beep on the buzzer
  #ifdef ENABLE_CONTROLLER
  getPower();
  // initialise the time to check the battery
  timeCheckBattery = millis() + TIME_CHECK_BATTERY;
  timeAntiLoop = millis() + TIME_ANTI_LOOP;
  #endif

  // initialise servo positions
  //setCagePosition(CAGE_DOWN);
  setCagePosition(CAGE_DOWN);

  
}

void loop()
{
  static int16_t home_heading;
  
  serialCommunication();
  
  #ifdef ENABLE_BLUETOOTH
    bluetoothCommunication();
  #endif
  #ifdef ENABLE_CONTROLLER
    batteryCheck();
  #endif
  static uint8_t test=0;
  
  if(enableAutoObstacleAvoidance)
  {
    // no desired direction, give 0 as argument
    
    //goHome(0);
    
  }
  if(goHomeValue)
  {
    //headHome(home_heading);
    goHome(50);
    //navigation_avoidance(6);
//    getHeading();
  //setMotorSpeed(100,100);
  delay(100);
  }
  
  if(enableSerialDumpIrValues)
  {
    Serial.print(getAnalogSensor(0));
    Serial.print("\t");
    Serial.print(getAnalogSensor(1));
    Serial.print("\t");
    Serial.print(getAnalogSensor(2));
    Serial.print("\t");
    Serial.println(getAnalogSensor(3));
    //Serial.println(determineWallSide());
    delay(100);
  }

  // start auto obstacle avoidance
  if(!digitalRead(BTN))
  {
      if (goHomeValue == 0)
      {
        goHomeValue = 1;
        play(440, 500);
        delay(1000);
        //home_heading = getDirection();
        //resetReturnBase();
        play(440, 500);
      }
      else
      {
        goHomeValue = 0;
        play(440, 500);
        delay(1000);
        //home_heading = getDirection();
        //resetReturnBase();
        resetReturnBase();
        setMotorSpeed(0,0);
        play(440, 500);
      }
  }


}

void batteryCheck()
{
  // check battery level and make a beep if it's too low
  if(millis() > timeCheckBattery)
  {
    getPower();
    if(batteryVoltage < CONST_BATTERY_LOW)
    {
      play(TONE_BATTERY, 500);
    }
    timeCheckBattery = millis() + TIME_CHECK_BATTERY;
  }
}
void setCagePosition(cage_positions position)
{
  servoRight.attach(S1);
  servoLeft.attach(S2);

  uint8_t r, l;

  if(position == CAGE_UP)
  {
    // both sevomotors have 160 steps between up and down positions, so this is allowed
    /*for(l = SERVO_LEFT_DOWN, r = SERVO_RIGHT_DOWN; r < SERVO_RIGHT_UP; r++, l--)
    {
      servoLeft.write(l);
      servoRight.write(r);
      delay(CONST_MAX_SERVO_SPEED);
    }*/
    cagePos = CAGE_UP;
  }
  else if(position == CAGE_DOWN)
  {
    /*for(l = SERVO_LEFT_UP, r = SERVO_RIGHT_UP; r > SERVO_RIGHT_DOWN; r--, l++)
    {
      servoLeft.write(l);
      servoRight.write(r);
      delay(CONST_MAX_SERVO_SPEED);
    }*/
    cagePos = CAGE_DOWN;
  }
  // always detach the motors so that they are free-running and do not consume power for nothing in resting positions
  servoLeft.detach();
  servoRight.detach();
}

uint16_t getAnalogSensor(uint8_t id)
{
  uint16_t value;
  switch(id)
  {
  case 0:
    value = analogRead(A0);
    break;
  case 1:
    value = analogRead(A1);
    break;
  case 2:
    value = analogRead(A2);
    break;
  case 3:
    value = analogRead(A3);
    break;
  case 4:
    value = analogRead(A4);
    break;
  case 5:
    value = analogRead(A5);
    break;
  default:
    value = 0;
  }
  return value;
}


void getPower()
{
  Wire.beginTransmission(I2C_MOTOR_CONTROLLER_ADDRESS);
  // casting needed for some reason
  uint8_t available = Wire.requestFrom((uint8_t)I2C_MOTOR_CONTROLLER_ADDRESS, (uint8_t)6);

  // read 6 bytes, 2 by 2, high byte first: voltage, left motor current, right motor current
  if(available == 6)
  {
    batteryVoltage = (Wire.read() << 8) | Wire.read();
    currentLeft = (Wire.read() << 8) | Wire.read();
    currentRight = (Wire.read() << 8) | Wire.read();
  }
  else
  {
    // inform i2c error
    play(TONE_I2C_ERROR, 500);
  }

  Wire.endTransmission();
}

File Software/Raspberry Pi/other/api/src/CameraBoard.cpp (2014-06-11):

/*
Copyright (c) 2013, Broadcom Europe Ltd
Copyright (c) 2013, James Hughes
All rights reserved.

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
THIS SOFTWARE IS PROVIDED BY THE COPYRIGHT HOLDERS AND CONTRIBUTORS "AS IS" AND
ANY EXPRESS OR IMPLIED WARRANTIES, INCLUDING, BUT NOT LIMITED TO, THE IMPLIED
WARRANTIES OF MERCHANTABILITY AND FITNESS FOR A PARTICULAR PURPOSE ARE
DISCLAIMED. IN NO EVENT SHALL THE COPYRIGHT HOLDER OR CONTRIBUTORS BE LIABLE FOR ANY
DIRECT, INDIRECT, INCIDENTAL, SPECIAL, EXEMPLARY, OR CONSEQUENTIAL DAMAGES
(INCLUDING, BUT NOT LIMITED TO, PROCUREMENT OF SUBSTITUTE GOODS OR SERVICES;
LOSS OF USE, DATA, OR PROFITS; OR BUSINESS INTERRUPTION) HOWEVER CAUSED AND
ON ANY THEORY OF LIABILITY, WHETHER IN CONTRACT, STRICT LIABILITY, OR TORT
(INCLUDING NEGLIGENCE OR OTHERWISE) ARISING IN ANY WAY OUT OF THE USE OF THIS
SOFTWARE, EVEN IF ADVISED OF THE POSSIBILITY OF SUCH DAMAGE.
*/
#include "CameraBoard.h"
#include "mmal/mmal_buffer.h"
#include "mmal/mmal_default_components.h"
#include "mmal/mmal_util.h"
#include "mmal/mmal_util_params.h"
#include <iostream>
#include <semaphore.h>
using namespace std;

static void control_callback(MMAL_PORT_T *port, MMAL_BUFFER_HEADER_T *buffer) {
	CAMERA_BOARD_USERDATA *userdata = (CAMERA_BOARD_USERDATA*)port->userdata;
	if (buffer->cmd == MMAL_EVENT_PARAMETER_CHANGED) {
	} else {
		// Unexpected control callback event!
		(userdata->unexpectedControlCallbacks)++;
	}
	mmal_buffer_header_release(buffer);
}

static void buffer_callback(MMAL_PORT_T *port, MMAL_BUFFER_HEADER_T *buffer) {
	CAMERA_BOARD_USERDATA *userdata = (CAMERA_BOARD_USERDATA*)port->userdata;
	if (userdata == NULL || userdata->cameraBoard == NULL) {
		
	} else {
		bool isRGB = userdata->cameraBoard->getEncoding() == CAMERA_BOARD_ENCODING_RGB;
		bool canCopy = true;
		if (userdata->offset + buffer->length >= userdata->length) {
			canCopy = false;
			if (userdata->errorStream)
				*userdata->errorStream << userdata->cameraBoard->API_NAME << ": Buffer provided was too small! Failed to copy data into buffer.\n";
			userdata->cameraBoard = NULL;
		}
		mmal_buffer_header_mem_lock(buffer);
		if (canCopy) {
			unsigned int i = (isRGB) ? 54 : 0;
			for (; i < buffer->length; i++, userdata->offset++) {
				userdata->data[userdata->offset] = buffer->data[i];
			}
		}
		mmal_buffer_header_mem_unlock(buffer);
		if ((buffer->flags & (MMAL_BUFFER_HEADER_FLAG_FRAME_END | MMAL_BUFFER_HEADER_FLAG_TRANSMISSION_FAILED)) != 0) {
			if (userdata->mutex == NULL) {
				userdata->imageCallback(userdata->data, userdata->startingOffset, userdata->length - userdata->startingOffset);
			} else {
				sem_post(userdata->mutex);
			}
		}
	}
	mmal_buffer_header_release(buffer);
	if (port->is_enabled) {
		MMAL_BUFFER_HEADER_T *new_buffer = mmal_queue_get(userdata->encoderPool->queue);
		if (new_buffer) mmal_port_send_buffer(port, new_buffer);
	}
}

void CameraBoard::setDefaults() {
	width = 640;
	height = 480;
	encoding = CAMERA_BOARD_ENCODING_BMP;
	encoder = NULL;
	encoder_connection = NULL;
	sharpness = 0;
	contrast = 0;
	brightness = 50;
	quality = 85;
	saturation = 0;
	iso = 400;
	//videoStabilisation = 0;
	//exposureCompensation = 0;
	exposure = CAMERA_BOARD_EXPOSURE_AUTO;
	metering = CAMERA_BOARD_METERING_AVERAGE;
	awb = CAMERA_BOARD_AWB_AUTO;
	imageEffect = CAMERA_BOARD_IMAGE_EFFECT_NONE;
	//colourEffects.enable = 0;
	//colourEffects.u = 128;
	//colourEffects.v = 128;
	rotation = 0;
	changedSettings = true;
	horizontalFlip = false;
	verticalFlip = false;
	//roi.x = params->roi.y = 0.0;
	//roi.w = params->roi.h = 1.0;
}
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

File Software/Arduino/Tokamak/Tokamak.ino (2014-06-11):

/***************************************************************************************
 *
 * Title:      STI competition Arduino code for the Tokamak robot.
 * Date:       2014-06-06
 *
 ***************************************************************************************/
#include <Servo.h>
#include <prismino.h>
#include <Wire.h>
#include "robot.h"

Tokamak robot;

// transition structure
struct transition
{
    enum state_codes state_source;
    enum return_codes return_code;
    enum state_codes state_destination;
};

// state functions and codes must be in sync
return_codes (*state[])(void) = {
  stateSearching,
  stateFetchingBottle,
  stateLowerCage,
  stateGoHome,
  stateRaiseCage
};

struct transition state_transitions[] = {
  {STATE_SEARCHING,       OK,     STATE_FETCHING_BOTTLE},
  {STATE_SEARCHING,       REPEAT, STATE_SEARCHING},
  {STATE_FETCHING_BOTTLE, OK,     STATE_LOWER_CAGE},
  {STATE_FETCHING_BOTTLE, REPEAT, STATE_FETCHING_BOTTLE},
  {STATE_FETCHING_BOTTLE, FAIL,   STATE_SEARCHING},
  {STATE_LOWER_CAGE,      OK,     STATE_GO_HOME},
  {STATE_GO_HOME,         REPEAT, STATE_GO_HOME},
  {STATE_GO_HOME,         OK,     STATE_RAISE_CAGE},
  {STATE_RAISE_CAGE,      OK,     STATE_SEARCHING}
};

enum state_codes currentState;
enum return_codes returnCode;
comm_methods inputMethod;

// pointer to the current called function in the state machine
return_codes (*stateFunction)(void);

// other global variables
volatile uint8_t bottlePosition;
volatile uint8_t bottleDistance;
sides sideWall;

volatile uint32_t timeBottleLastSeen;
volatile uint32_t timeNextBottleCheck;
uint32_t timeCheckBattery;
volatile boolean booleanBottleUpdate;
boolean booleanBottleSecondTry;
boolean booleanFalseBottle;

// ############################################################ SETUP

void setup()
{
  // set pin output mode (sources current)
  pinMode(LED, OUTPUT);
  pinMode(PIN_LIGHTS, OUTPUT);
  
  // enable button pull-up
  pinMode(BTN, INPUT);
  digitalWrite(BTN, HIGH);

  // play a sound on boot, repeated sounds will indicate very low battery voltage
  robot.playSound(ONEUP);

  // initialise serial bus for communication with the Raspberry Pi
  Serial.begin(9600);

  // initialise the bus for communication with the computer via Bluetooth
  #ifdef ENABLE_BLUETOOTH
  Bluetooth.begin(9600);
  #endif

  // join i2c bus as master
  Wire.begin();
  // disable internal pull-ups to 5V as there are external 2K pull-ups to 3.3V
  digitalWrite(SDA, LOW);
  digitalWrite(SCL, LOW);
  
  #ifdef ENABLE_COMPASS
  // wait for the imu to boot
  delay(500);
  // put the HMC5883 IC into the correct operating mode
  // open communication with HMC5883
  Wire.beginTransmission(I2C_COMPASS_ADDRESS);
  // select mode register
  Wire.write(0x02);
  // continuous measurement mode
  Wire.write(0x00);
  Wire.endTransmission();
  #endif
  
  // initialise global variables
  bottlePosition = 0;
  bottleDistance = 0;
  
  timeCheckBattery = millis() + TIME_CHECK_BATTERY;
  timeBottleLastSeen = 0;
  
  sideWall = RIGHT;
  booleanBottleUpdate = 0;
  
  // reset the robot state
  reset();
  
  currentState = ENTRY_STATE;
}

// ############################################################ MAIN LOOP

void loop()
{
  if(Serial.available())
  {
    processInput(USB);
  }
  
  #ifdef ENABLE_BLUETOOTH
  if(Bluetooth.available())
  { 
    processInput(BLUETOOTH);
  }
  #endif
  
  uint16_t irLeft, irCenterLeft, irCenterRight, irRight;
  robot.readIrSensors(&irLeft, &irCenterLeft, &irCenterRight, &irRight);
  
  Bluetooth.print(irLeft);
  Bluetooth.print("\t");
  Bluetooth.print(irCenterLeft);
  Bluetooth.print("\t");
  Bluetooth.print(irCenterRight);
  Bluetooth.print("\t");
  Bluetooth.println(irRight);
  
  //Bluetooth.println(robot.getHeading());
  
  // toggle robot running state via the button on the shield
  if(!digitalRead(BTN))
  {
    robot.playSound(POWERUP);
    robot.flags.running = !robot.flags.running;
    
    // robot has been stopped
    if(!robot.flags.running)
    {
      robot.stop();
      // reset robot state to ENTRY_STATE
      currentState = ENTRY_STATE;
    }
    
    // wait for button debounce
    delay(1000);
  }

  #ifdef ENABLE_CONTROLLER
  // check battery level and make a beep if it's too low
  if(millis() > timeCheckBattery)
  {
    robot.checkBattery();
  }
  #endif
  
  if(robot.flags.running)
  {
    // current function to call according to the state machine
    stateFunction = state[currentState];
    // actually call the function
    returnCode = stateFunction();
    // fetch next state
    currentState = lookupTransitions(currentState, returnCode);
  }
}

// ############################################################ STATE TRANSITIONS

// returns the new state according to the current state and the return value
state_codes lookupTransitions(state_codes state, return_codes code)
{
  uint8_t i;
  // default return state is the entry state
  state_codes nextState = ENTRY_STATE;
  // see if a state transition matches and switch to the next state
  for(i = 0; i < sizeof(state_transitions) / sizeof(transition); i++)
  {
    if(state_transitions[i].state_source == state && state_transitions[i].return_code == code)
    {
      nextState = state_transitions[i].state_destination;
      if(nextState != state_transitions[i].state_source)
      {
        robot.playSound(COIN);
      }
      break;
    }
  }
  return nextState;
}

// ############################################################ ROBOT STATES

return_codes stateSearching()
{
  // check if a bottle has been seen and change state
  if(bottlePosition && millis() > timeNextBottleCheck)
  {
    robot.stop();
    booleanBottleSecondTry = 0;
    booleanFalseBottle = 1;
    return OK;
  }
  
  // make robot roam the arena set deviation to 0 to go straight when there are no obstacles
  robot.headTo(0);
  
  return REPEAT;
}
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

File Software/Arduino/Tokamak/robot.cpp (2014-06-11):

/***************************************************************************************
 *
 * Title:      STI competition Arduino code for the Tokamak robot
 * Date:       2014-06-06
 *
 ***************************************************************************************/
#include <Servo.h>
#include <Wire.h>
#include <prismino.h>
#include "robot.h"
#include "pitch.h"
#include "sound.h"

Tokamak::Tokamak()
{
  // initialise default values
  this->flags.enableFrontLeds = false;
  this->flags.running = false;
  this->flags.cagePosition = CAGE_UP;
}

void Tokamak::setCagePosition(cage_positions position)
{
  this->servoRight.attach(S1);
  this->servoLeft.attach(S2);

  uint8_t r, l;

  if(position == CAGE_UP)
  {
    // both sevomotors have 160 steps between up and down positions, so this is allowed
    for(l = SERVO_LEFT_DOWN, r = SERVO_RIGHT_DOWN; r < SERVO_RIGHT_UP; r++, l--)
    {
      this->servoLeft.write(l);
      this->servoRight.write(r);

      delay(CONST_MAX_SERVO_SPEED);
    }
  }
  else if(position == CAGE_DOWN)
  {
    for(l = SERVO_LEFT_UP, r = SERVO_RIGHT_UP; r > SERVO_RIGHT_DOWN; r--, l++)
    {
      this->servoLeft.write(l);
      this->servoRight.write(r);

      delay(CONST_MAX_SERVO_SPEED);
    }
    
  }

  // always detach the motors so that they are free-running and do not consume power in resting positions
  this->servoLeft.detach();
  this->servoRight.detach();
  
  this->flags.cagePosition = position;
}

void Tokamak::setSpeed(int8_t speedLeft, int8_t speedRight)
{
  // controller has been disabled
  #ifndef ENABLE_CONTROLLER
  return;
  #endif
  
  Wire.beginTransmission(I2C_MOTOR_CONTROLLER_ADDRESS);
  Wire.write("s");

  // make sure not to go over the maximum speed limit (100 or -100)
  if(speedLeft > CONST_SPEED_MAX)
  {
    Wire.write(CONST_SPEED_MAX);
  }
  else if(speedLeft < -CONST_SPEED_MAX)
  {
    Wire.write(-CONST_SPEED_MAX);
  }
  else
  {
    Wire.write(speedLeft);
  }

  if(speedRight > CONST_SPEED_MAX)
  {
    Wire.write(CONST_SPEED_MAX);
  }
  else if(speedRight < -CONST_SPEED_MAX)
  {
    Wire.write(-CONST_SPEED_MAX);
  }
  else
  {
    Wire.write(speedRight);
  }

  Wire.endTransmission();
  
  // a small delay is needed so that the speed could actually be applied to the wheels
  delay(CONST_SPEED_SET_DELAY);
}

void Tokamak::stop()
{
  this->setSpeed(0, 0);
}

void Tokamak::checkBattery()
{
  Wire.beginTransmission(I2C_MOTOR_CONTROLLER_ADDRESS);
  
  // casting needed for some reason
  uint8_t available = Wire.requestFrom((uint8_t)I2C_MOTOR_CONTROLLER_ADDRESS, (uint8_t)6);

  // read 6 bytes, 2 by 2, high byte first: voltage, left motor current, right motor current
  if(available == 6)
  {
    this->batteryVoltage = (Wire.read() << 8) | Wire.read();
    this->currentLeft = (Wire.read() << 8) | Wire.read();
    this->currentRight = (Wire.read() << 8) | Wire.read();
  }
  else
  {
    // inform i2c error
    play(TONE_I2C_ERROR, 500);
  }

  Wire.endTransmission();
  
  if(this->batteryVoltage < CONST_BATTERY_LOW)
  {
    play(TONE_BATTERY, 500);
  }
}

void Tokamak::setLights(boolean state)
{
  digitalWrite(PIN_LIGHTS, state);
}

int16_t Tokamak::getHeading()
{
  #ifndef ENABLE_COMPASS
  return 0;
  #endif
  
  int16_t x = 0, y = 0, z = 0;
  
  Wire.beginTransmission(I2C_COMPASS_ADDRESS);
  // select register 3, X MSB register
  Wire.write(0x03);
  Wire.endTransmission();

  Wire.requestFrom(I2C_COMPASS_ADDRESS, 6);
  if(6 <= Wire.available())
  {
    x = (Wire.read() << 8) | Wire.read();
    z = (Wire.read() << 8) | Wire.read();
    y = (Wire.read() << 8) | Wire.read();
  }
  else
  {
    // inform i2c error
    play(TONE_I2C_ERROR, 500);
    return 0;
  }
  
  int16_t angle = atan2(x, z) * 180 / M_PI;
  return angle;
}

void Tokamak::turn(int16_t deviation, int8_t speed)
{
  int8_t speedLeft = 0;
  int8_t speedRight = 0;
  
  // limit deviation to maximum allowed speed
  if(deviation > speed)
  {
    deviation = speed;
  }
  else if(deviation < -speed)
  {
    deviation = -speed;
  }
  
  if(deviation < -CONST_DEVIATION_OK)
  {
    speedLeft = speed;
    speedRight = -speed;
  }
  else if(deviation > CONST_DEVIATION_OK)
  {
    speedLeft = -speed;
    speedRight = speed;
  }
  else
  {
    speedLeft = 0;
    speedRight = 0;
  }
  
  this->setSpeed(speedLeft, speedRight);
}

void Tokamak::headTo(int16_t deviation, int8_t speed)
{
  navigation_avoidance(deviation);
  return;
  
  /*int8_t speedLeft = 0;
  int8_t speedRight = 0;
  
  uint16_t irLeft, irCenterLeft, irCenterRight, irRight;
  this->readIrSensors(&irLeft, &irCenterLeft, &irCenterRight, &irRight);
  
  // these values are incremented over time and reset after every TIME_ANTI_LOOP seconds
  static uint8_t antiLoopCountLeft = 0, antiLoopCountRight = 0;
  static uint32_t timeAntiLoop = 0;
  
  // every TIME_ANTI_LOOP seconds reset the anti-loop timer and wheel counters
  if(millis() > timeAntiLoop)
  {
    // every TIME_ANTI_LOOP seconds reset the anti-loop timer and wheel counters
    antiLoopCountLeft = 0;
    antiLoopCountRight = 0;
    timeAntiLoop = millis() + TIME_ANTI_LOOP;
  }
  
  // limit deviation to maximum allowed speed
  if(deviation > speed)
  {
    deviation = speed;
  }
  else if(deviation < -speed)
  {
    deviation = -speed;
  }
  
  // check if the robot has entered an infinite loop
  if(antiLoopCountLeft > CONST_LOOP_TURN_TIMES && antiLoopCountRight > CONST_LOOP_TURN_TIMES)
  {
    // if the cage is deployed reverse a bit
    if(this->flags.cagePosition == CAGE_UP)
    {
      this->setSpeed(-speed, -speed);
      delay(500);
    }
    
    // set speed immediately
    if(deviation > 0)
    {
      this->setSpeed(speed, -speed);
    }
    else
    {
      this->setSpeed(-speed, speed);
    }
    
    delay(TIME_ANTI_LOOP_TIMEOUT_TURN);
    
    // reset the counters
    antiLoopCountLeft = 0;
    antiLoopCountRight = 0;
  }
  // avoid obstacles using the IR sensors
  else if(irCenterRight > CONST_IR_OBSTACLE_CENTER_CAGE)
  {
    // turn on itself
    speedLeft = speed;
    speedRight = -speed;
    antiLoopCountLeft++;
  }
  else if(irCenterLeft > CONST_IR_OBSTACLE_CENTER_CAGE)
  {
    speedLeft = -speed;
    speedRight = speed;
    antiLoopCountRight++;
  }
  else if(irRight > CONST_IR_OBSTACLE_SIDE_CAGE)
  {
    // block one wheel, reverse the other
    speedLeft = -speed;
    speedRight = 0;
    antiLoopCountLeft++;
  }
  else if(irLeft > CONST_IR_OBSTACLE_SIDE_CAGE)
  {
    speedLeft = 0;
    speedRight = -speed;
    antiLoopCountRight++;
  }
  else if(deviation < -CONST_DEVIATION_OK)
  {
    speedLeft = speed;
    speedRight = speed + deviation;
  }
  else if(deviation > CONST_DEVIATION_OK)
  {
    speedLeft = speed - deviation;
    speedRight = speed;
  }
  else
  {
    // simply go forwards
    speedLeft = speed;
    speedRight = speed;
  }
  
  this->setSpeed(speedLeft, speedRight);*/
}
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

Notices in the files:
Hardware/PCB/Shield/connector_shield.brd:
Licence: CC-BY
